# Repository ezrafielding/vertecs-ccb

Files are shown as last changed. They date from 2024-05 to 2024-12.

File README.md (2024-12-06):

# VERTECS Camera Control Board

[](https://github.com/ezrafielding/vertecs-ccb/blob/main/LICENSE)



VERTECS Mission Patch VERTECS Logo

Welcome to the VERTECS Camara Control Board (CCB) project! This is an open-source hardware project designed to provide a flexible and robust payload interface for 6U nanosatellites.

## Introduction
The VERTECS CCB, is an open-source payload interface board leveraging Commercial Off-The-Shelf (COTS) components with a Raspberry Pi Compute Module 4 at its core. Originally developed for the [VERTECS 6U Astronomical Nanosatellite](https://www.vertecs-project.com), the board has been opened-sourced and made available for use in future nanosatellite projects.

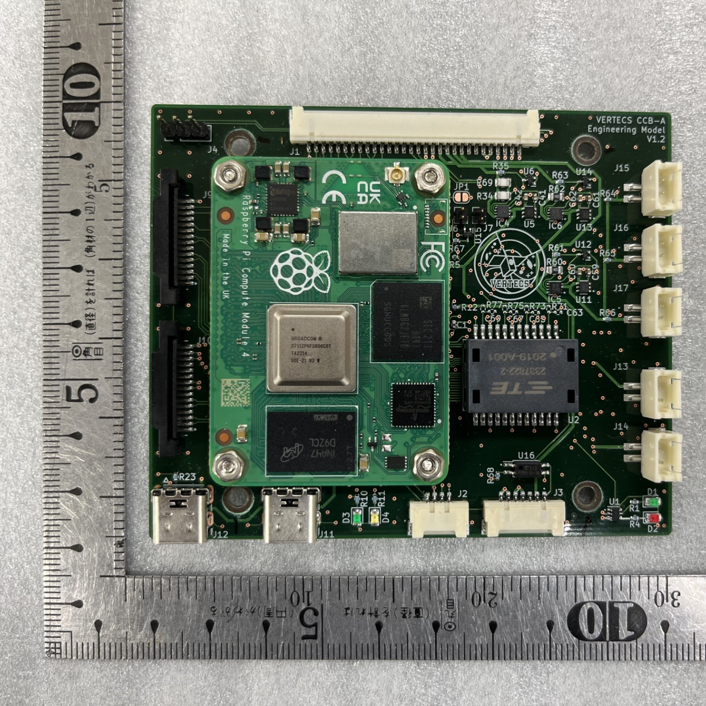
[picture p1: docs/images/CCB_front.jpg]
CCB Front
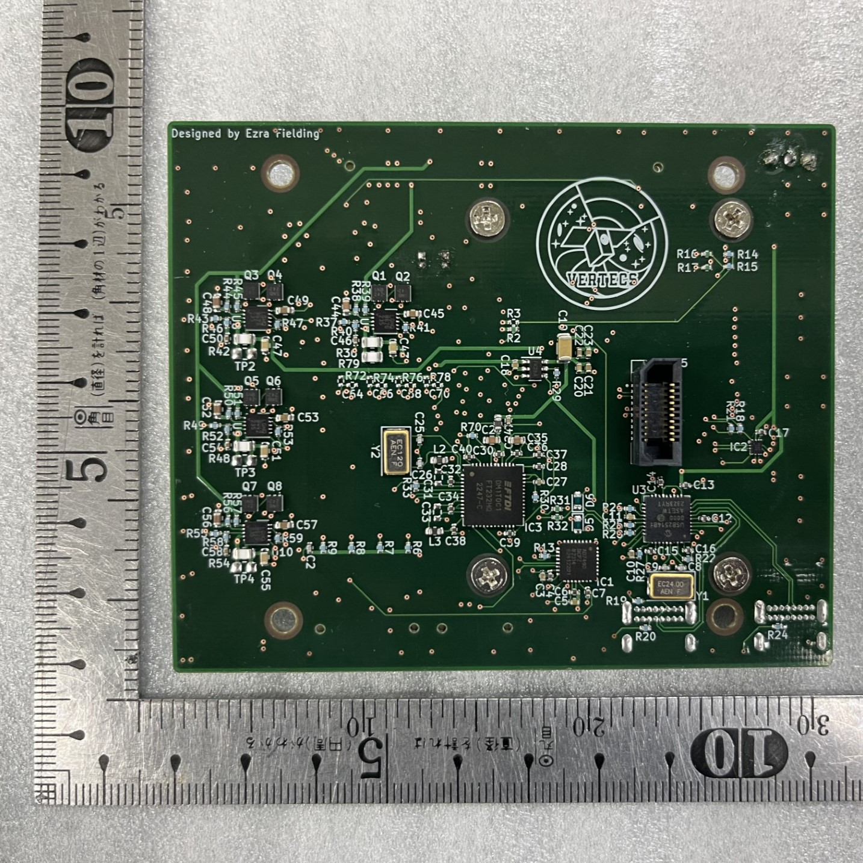
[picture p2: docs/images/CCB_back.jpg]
CCB Back
 

More information can be found in the [conference paper](https://doi.org/10.1117/12.3019471) for the VERTECS CCB.

## Getting Started
### Prerequisites
- [KiCAD 7](https://www.kicad.org/) installed to access PCB design files.

### Setup
1. Clone the repository:
   ```bash
   git clone https://github.com/ezrafielding/vertecs-ccb.git
   ```
2. Open the KiCAD project file in the VERTECS_CCB directory.

## Citation
Ezra Fielding, Victor H. Schulz, Keenan A. A. Chatar, Kei Sano, Akitoshi Hanazawa, "VERTECS: A COTS-based payload interface board to enable next generation astronomical imaging payloads," Proc. SPIE 13101, Software and Cyberinfrastructure for Astronomy VIII, 131010J (25 July 2024); https://doi.org/10.1117/12.3019471

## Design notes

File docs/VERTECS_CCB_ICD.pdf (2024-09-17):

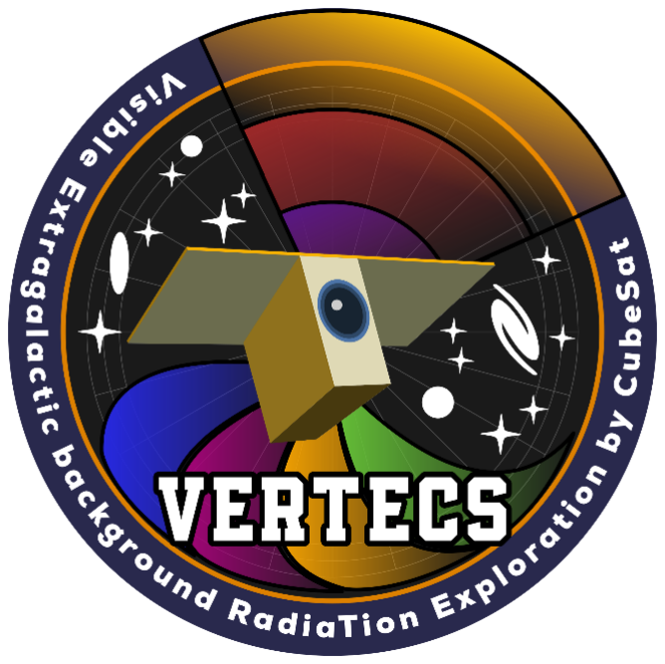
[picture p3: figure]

# VERTECS Interface Control Document Camera Control Board Subsystem

# 1. Overview of the subsystem

## 1.1. Subsystem Overview

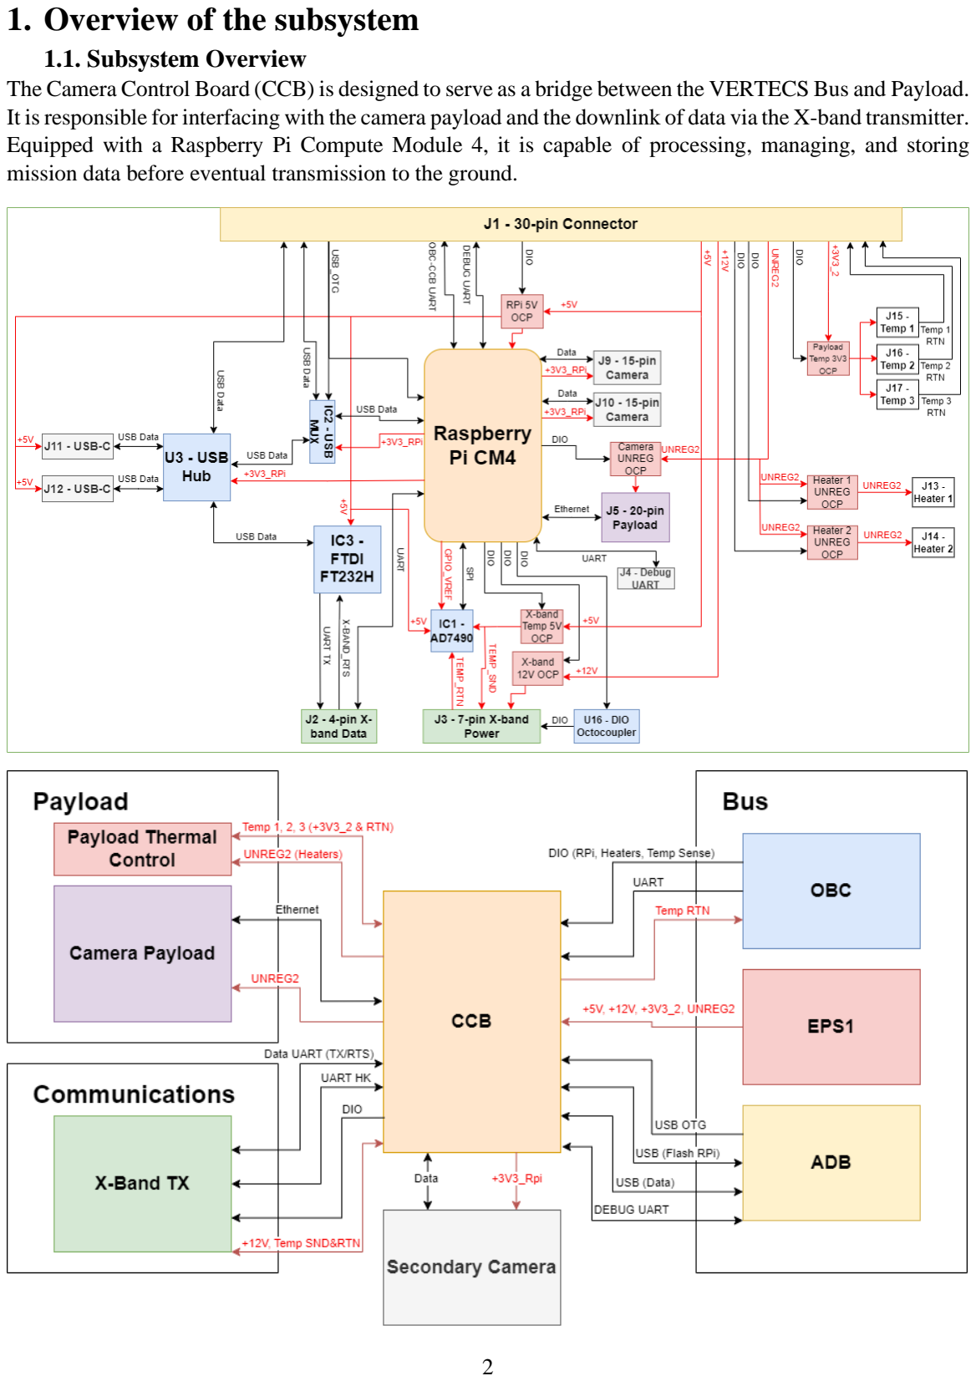
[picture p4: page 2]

The Camera Control Board (CCB) is designed to serve as a bridge between the VERTECS Bus and Payload. It is responsible for interfacing with the camera payload and the downlink of data via the X-band transmitter. Equipped with a Raspberry Pi Compute Module 4, it is capable of processing, managing, and storing mission data before eventual transmission to the ground.

## 1.2. General Requirements

- SR-CCB1: CCB shall control the mission payload camera, including status check, power line check, exposure, and data collection.
- SR-CCB2: CCB shall control the secondary camera, including status check, power line check, exposure, and data collection.
- SR-CCB3: CCB is responsible for all the data transfer to the X-band transmitter.

## 1.3. Performance Requirements

- SR-CCB4: CCB can send data to the X-band transmitter at a speed higher than 5 Mbps.
- SR-CCB5: CCB shall have the data storage capacity for three-day observation data.

## 1.4. General Specifications

The CCB includes a Raspberry Pi CM4 with 32GB of EMMC flash storage and 8GB of RAM. Power and a gigabit ethernet connection, via the built-in networking capabilities of the CM4, are provided to the main camera payload through a 20-pin surface connector. To enable high-speed data transfer to the X-band transmitter, the CCB includes an FTDI FT232H UART chip connected to the CM4 via USB. Two USB-C ports are included on the CCB to allow for easier development, as well as additional payload capabilities for the satellite. Two 15-pin CSI camera connectors allow CSI cameras to be connected to the CM4. The main connection to the satellite bus is done over a 30-pin harness. Three 2-pin connections for temperature and two 2-pin connections for heaters are provided on the CCB for control by the main satellite Bus system.

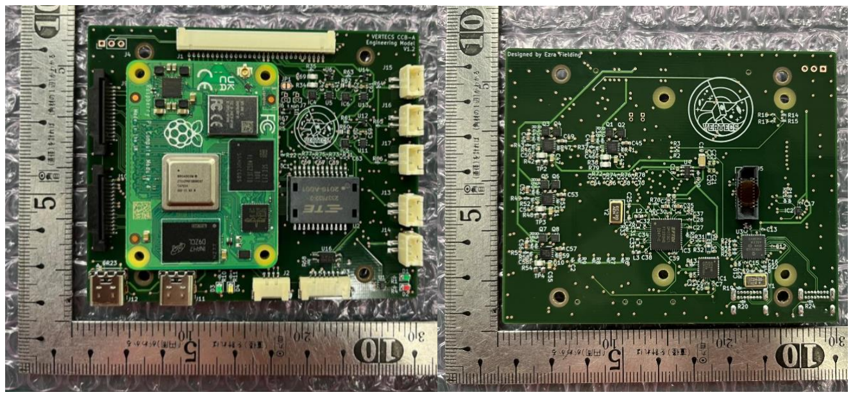
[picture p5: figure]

# 2. Mechanical Interface

## 2.1. Dimensions

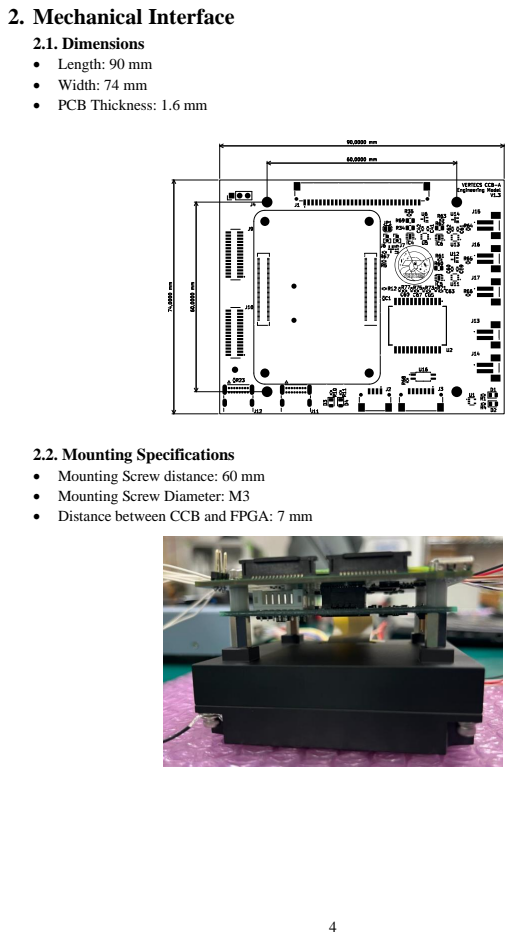
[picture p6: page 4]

• Length: 90 mm
• Width: 74 mm
• PCB Thickness: 1.6 mm

2.2. Mounting Specifications
• Mounting Screw distance: 60 mm
• Mounting Screw Diameter: M3
• Distance between CCB and FPGA: 7 mm

# 3. Thermal Interface

The operating and storage temperature ranges (where available from the manufacturer) for mission critical ICs and components are given in the table below.

Part Reference | Part Number | Part Description | Operating Temperature (°C) | Storage Temperature (°C)
Module 1 | Raspberry Pi CM4 | Raspberry Pi CM4 | -20 to +85 | -
U2 | 2337822-2 | Ethernet Magnetics | -40 to +105 | -40 to +85
IC1 | AD7490B | ADC | -40 to +85 | -65 to +150
IC2 | FSUSB42 | USB MUX | -40 to +85 | -65 to +150
U3 | USB2514B-I | USB Hub | -40 to +85 | -55 to +150
IC3 | FT232HQ | FTDI UART | -40 to +85 | -65 to +150
Considering the above information, the nominal operating temperature range for the CCB shall be -20°C to +85°C. Operation outside this range is possible, but performance and longevity cannot be guaranteed without further testing.

6

# 4. Electrical Interface

## 4.1. Pin Assignment

## J1 – 30-pin Connector to Backplane (Hirose DF14-30P-1.25H(35))

30-pin Connector
Pin No | Connection Name | Connector type | Voltage level | Max Current | Frequency / Baud Rate | Protocol | Comments
1 | OBC-CCB_PWR_ON_DIO (MainPIC_to_CCB) | 30-pin | 3V3 | - | - | - | OCP control for ON/OFF of RPi
2 | OBC-CCB_UART (MainPIC_to_CCB) | 30-pin | 3V3 | - | 115200 | RS232 | Data receive from OBC
3 | CCB-OBC_UART (CCB_to_MainPIC) | 30-pin | 3V3 | - | 115200 | RS232 | Data send to OBC
4 | ADB-CCB_UART (ADB_to_CCB) | 30-pin | 3V3 | | 115200 | RS232 | CCB Serial Terminal from ADB
5 | CCB-ADB_UART (CCB_to_ADB) | 30-pin | 3V3 | - | 115200 | RS232 | CCB Serial Terminal to ADB
6 | CCB-ADB_USBD0_P | 30-pin | 3V3 | - | 480Mbps | USB | For programming over USB-C
7 | CCB-ADB_USBD0_N | 30-pin | 3V3 | - | 480Mbps | USB | For programming over USB-C
8 | CCB-ADB_USBOTG | 30-pin | 5V | - | - | - | For enabling programming over USB-C
9 | CCB-ADB_USBD1_P | 30-pin | 3V3 | - | 480Mbps | USB | For RPi USB data access
10 | CCB-ADB_USBD1_N | 30-pin | 3V3 | - | 480Mbps | USB | For RPi USB data access
11 | CCB-TEMP_DIO | 30-pin | 3V3 | - | - | - | OCP control for ON/OFF of Temp Sensors
12 | CCB-TEMP_ANALOG1 | 30-pin | 3V3 | 1A | - | - | Analogue reading for temp sensor
13 | CCB-TEMP_ANALOG2 | 30-pin | 3V3 | 1A | - | - | Analogue reading for temp sensor
14 | CCB-TEMP_ANALOG3 | 30-pin | 3V3 | 1A | - | - | Analogue reading for temp sensor
15 | CCB-HEATER_1_DIO | 30-pin | 3V3 | - | - | - | OCP control for ON/OFF of Heater 1
16 | CCB-HEATER_2_DIO | 30-pin | 3V3 | - | - | - | OCP control for ON/OFF of Heater 2
17 | GND | 30-pin | 0 | | - | - | GND
18 | GND | 30-pin | 0 | | - | - | GND
19 | SUP_5V0 | 30-pin | 5V | 3A | - | - | 5V line to power RPi
20 | SUP_5V0 | 30-pin | 5V | 3A | - | - | 5V line to power RPi
21 | SUP_3V3_2 | 30-pin | 3V3 | 1A | - | - | 3.3V for Temperature Sensors
22 | SUP_3V3_2 | 30-pin | 3V3 | 1A | - | - | 3.3V for Temperature Sensors
23 | SUP_UNREG_2 | 30-pin | 8V4 (max) | 4A | - | - | UNREG line for CAM and Heaters
24 | SUP_UNREG_2 | 30-pin | 8V4 (max) | 4A | - | - | UNREG line for CAM and Heaters
25 | SUP_12V0 | 30-pin | 12V | 3A | - | - | 12V line for X-band
26 | SUP_12V0 | 30-pin | 12V | 3A | - | - | 12V line for X-band
27 | GND | 30-pin | 0 | | - | - | GND
28 | GND | 30-pin | 0 | | - | - | GND
29 | NC* | 30-pin | | | | | Tied to GND
30 | NC* | 30-pin | | | | | Tied to GND
*NC pins are tied to GND

7

## J2 – 4-pin Connector to X-band Data (Hirose DF14-4P-1.25H(35))

4-pin Connector (X-band)

Pin No | Connection Name | Connector type | Voltage level | Max Current | Frequency / Baud Rate | Protocol | Comments
1 | XBAND_CONFIG | 4-pin | 3V3 | - | 115200 | RS232 | Configure X-band
2 | XBAND_HK | 4-pin | 3V3 | - | 115200 | RS232 | HK Data receive from X-band
3 | XBAND_RTS | 4-pin | 3V3 | - | - | - | X-band RTS
4 | XBAND_IN | 4-pin | 3V3 | - | 12000000 | RS232 | Data send to X-band

## J3 – 7-pin Connector to X-band Power (Hirose DF14-7P-1.25H(35))

7-pin Connector (X-band)

Pin No | Connection Name | Connector type | Voltage level | Max Current | Frequency / Baud Rate | Protocol | Comments
1 | XBAND_DIO | 7-pin | 12V | - | - | - | X-Band direct ON/OFF control
2 | XBAND_TEMP_SND | 7-pin | 5V | 1A | - | - | X-Band analogue temperature power send
3 | XBAND_TEMP_RTN | 7-pin | 5V | 1A | - | - | X-Band analogue temperature return
4 | SUP_12V0 | 7-pin | 12V | 1.5A | - | - | 12V power to X-band
5 | SUP_12V0 | 7-pin | 12V | 1.5A | - | - | 12V power to X-band
6 | GND | 7-pin | 0 | - | - | - | GND
7 | GND | 7-pin | 0 | - | - | - | GND

## J4 – 3-pin Header for Debug Terminal UART

3-pin Header (UART)

Pin No | Connection Name | Connector type | Voltage level | Max Current | Frequency / Baud Rate | Protocol | Comments
1 | CCB_TX | 3-pin | 3V3 | - | 115200 | RS232 | CCB Debug UART TX
2 | CCB_RX | 3-pin | 3V3 | - | 115200 | RS232 | CCB Debug UART RX
3 | GND | 3-pin | 0 | - | - | - | GND

8

## J5 – 20-pin Connector to Payload (Hirose ER8-20S-0.8SV-5H)

20-pin Connector (Payload)
Pin No | Connection Name | Connector type | Voltage level | Max Current | Frequency / Baud Rate | Protocol | Comments
1 | GND | 20-pin | 0 | - | | | GND
2 | GND | 20-pin | 0 | - | | | GND
3 | TX0_P | 20-pin | 12V | - | 1Gbps | Ethernet | Digital interface to CAM
4 | GND | 20-pin | 0 | - | | | GND
5 | TX0_N | 20-pin | 12V | - | 1Gbps | Ethernet | Digital interface to CAM
6 | TX1_P | 20-pin | 12V | - | 1Gbps | Ethernet | Digital interface to CAM
7 | GND | 20-pin | 0 | - | | | GND
8 | TX1_N | 20-pin | 12V | - | 1Gbps | Ethernet | Digital interface to CAM
9 | TX2_P | 20-pin | 12V | - | 1Gbps | Ethernet | Digital interface to CAM
10 | GND | 20-pin | 0 | - | | | GND
11 | TX2_N | 20-pin | 12V | - | 1Gbps | Ethernet | Digital interface to CAM
12 | TX3_P | 20-pin | 12V | - | 1Gbps | Ethernet | Digital interface to CAM
13 | GND | 20-pin | 0 | - | | | GND
14 | TX3_N | 20-pin | 12V | - | 1Gbps | Ethernet | Digital interface to CAM
15 | NC
16 | GND | 20-pin | 0 | - | | | GND
17 | NC
18 | NC
19 | UNREG_2 | 20-pin | 8V4 (max) | 2A | - | - | PWR for CAM FPGA
20 | UNREG_2 | 20-pin | 8V4 (max) | 2A | - | - | PWR for CAM FPGA

## J9 – 15-pin Connector to Secondary Camera (TE Connectivity 1-1734248-5)

15-pin Connector (Secondary Camera)
Pin No | Connection Name | Connector type | Voltage level | Max Current | Frequency / Baud Rate | Protocol | Comments
1 | GND | 15-pin | 0 | - | - | - | GND
2 | CAM0_D0_N | 15-pin | 3V3 | - | - | Camera | Camera Data Line
3 | CAM0_D0_P | 15-pin | 3V3 | - | - | Camera | Camera Data Line
4 | GND | 15-pin | 0 | - | - | - | GND
5 | CAM0_D1_N | 15-pin | 3V3 | - | - | Camera | Camera Data Line
6 | CAM0_D1_P | 15-pin | 3V3 | - | - | Camera | Camera Data Line
7 | GND | 15-pin | 0 | - | - | - | GND
8 | CAM0_C_N | 15-pin | 3V3 | - | - | Camera | Camera Clock Line
9 | CAM0_C_P | 15-pin | 3V3 | - | - | Camera | Camera Clock Line
10 | GND | 15-pin | 0 | - | - | - | GND
11 | CAM_GPIO | 15-pin | 3V3 | - | - | - | Camera enable line from CM4
12 | NC | 15-pin | | | - | -
13 | SCL1 | 15-pin | 3V3 | - | - | I2C | I2C Clock Line
14 | SDA1 | 15-pin | 3V3 | - | - | I2C | I2C Data Line
15 | +3.3v | 15-pin | 3V3 | 600mA | - | - | +3.3v from CM4

9

## J13 to J17 – 2-pin for Heater Power and Payload Temperature Sensors (Molex 55460-0272)

2-pin Connector (Heater) x2

Pin No | Connection Name | Connector type | Voltage level | Max Current | Frequency / Baud Rate | Protocol | Comments
1 | UNREG_2 | 2-pin | 8V4 (max) | 2A | - | - | UNREG PWR for Heater
2 | GND | 2-pin | 0 | - | - | - | GND

2-pin Connector (Temperature Sensor) x3

Pin No | Connection Name | Connector type | Voltage level | Current | Frequency / Baud Rate | Protocol | Comments
1 | GND | 2 pin molex | 0 | - | - | - | GND
2 | TEMP_READ | 2 pin molex | 3V | 1A | - | - | Analogue reading for temp sensor

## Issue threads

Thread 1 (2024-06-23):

Consider adding a hardware-specific license

parker-research, 2024-06-23:
Very neat project!

Consider adding a hardware-specific, like the [CERN-OHL-P-2.0 Open Hardware License](https://choosealicense.com/licenses/cern-ohl-p-2.0/)! The MIT License is technically only applicable for software.

Good comparison/list of some options: https://choosealicense.com/non-software/

ezrafielding, 2024-06-23:
Great suggestion, thanks!
I've gone ahead and changed to the hardware-specific license.

parker-research, 2024-06-23:
Very awesome! :)

Is there a software component of this that'll be shared in the future?

ezrafielding, 2024-06-24:
We may release a software component some time in future when mission software is complete. Many of the commands we need to issue over the software are proprietary. But maybe we'll make a release of basic example functions. We do already mention what to expect with software in the associated paper (Raspberry Pi OS Lite as the OS and Python and C for mission software).

A BOM for off-board components also sounds like a great idea. Hopefully I can get around to that in the near future. I'll need to figure out what of those are actually publicly available. For now, I'd recommend checking the data sheets of each connector for the appropriate plug to use with it, and comparing that to the schematic for what to connect where. (The paper also has some nice pictures showing how everything plugs in together)

Closed 2024-06-23.

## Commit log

2024-05-29 Added CCB v1.3
    [12v_power.kicad_sch, 5v_power.kicad_sch, FTDI.kicad_sch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]
2024-09-17 Update to v1.4
    [FTDI.kicad_sch, VERTECS_CCB_A.kicad_pcb, VERTECS_CCB_A.kicad_sch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]
